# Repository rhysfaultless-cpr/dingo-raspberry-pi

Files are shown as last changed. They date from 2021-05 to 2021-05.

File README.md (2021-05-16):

# dingo-raspberry-pi
Installing a Raspberry Pi 4 on Clearpath Robotics Dingo

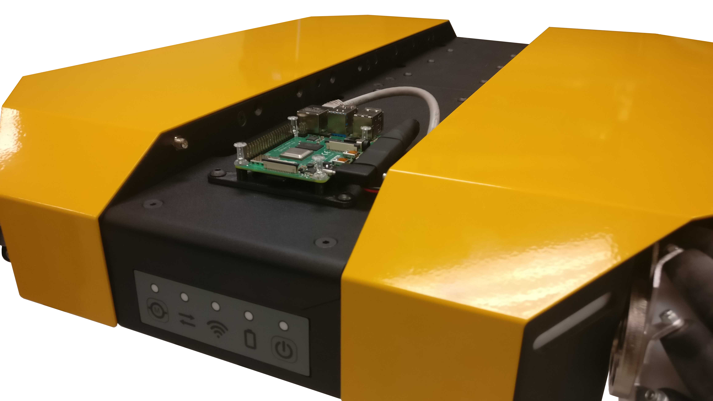
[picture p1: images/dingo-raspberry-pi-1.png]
Image of dingo and pi


Dingo is an indoor mobile robot that can be configured for differential-drive, or omnidrirectional-drive.
You can find more information about Dingo at the [Clearpath Robotics](https://clearpathrobotics.com/dingo-indoor-mobile-robot/) website.

## Hardware Overview

We mounted the Raspberry Pi 4 on the outside of the Dingo.
We conisdered this an advantage for the applications that want a low cost computer for Dingo.
The external mounting improves the Pi's WiFi signal, and gives quick access to the Pi's microSD card.

### Tools

You will need these tools:

* Wire stripper
* Wire cutter
* Crimper for Molex mini-fit-jr, 18 AWG crimps
* Hex key, 3 mm across flats

### Parts
| Quantity | CPR item number | Description | Manufacturer | Manufacturer # | Supplier | Supplier # |
| :---: | :--- | :--- | :--- | :--- | :--- | :--- |
| 1 | 021604 | microSD, 64 GB | Samsung | MB-ME64HA/AM | Amazon | B08879MG33 |
| 1 | 021758 | Cable—Ethernet, 2X RJ45, 300 | Monoprice | 13518 | — | — |
| 1 | 024011 | Bracket— Raspberry Pi | — | — | — | — |
| 4 | 024049 | Pin, Push | Westcott | 165841638 | Amazon | B003M5MTWC |
| 1 | 024051 | Computer, Single Board—Raspberry Pi 4, 4 GB | Raspberry Pi Foundation | Raspberry Pi 4 Model B, 4 GB | — | — |
| 1 | 024056 | Cable Assembly—USB-C X Molex | — | — | — | — |

#### 024011 Bracket— Raspberry Pi

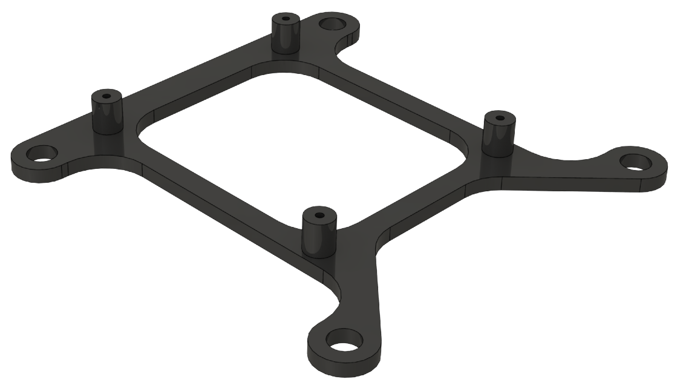
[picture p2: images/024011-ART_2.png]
Image of pi mounting bracket


This is a 3D printed bracket to hold the Pi on top of the Dingo. 
We printed our bracket in-house using PLA filament. ( fused deposition modeling, using polylactic acid filament )
A STEP214 model of this bracket is included in this repository as 024011-GEO_1.STL

#### 024056 Cable Assembly—USB-C X Molex 
(Raspberry Pi 4 Power Cable )

| Quantity | CPR item number | Description | Manufacturer | Manufacturer # | Supplier | Supplier # |
| :---: | :--- | :--- | :--- | :--- | :--- | :--- |
| 1 | 022206 | Connector, Housing | Molex | 39-01-2045 | Digi-Key | WM23701-ND |
| 2 | 022252 | Terminal, Crimp | Molex | 40-13-0852 | Digi-Key | WM24935-ND |
| 1 | 024192 | Cable—Barrel | Tensility | 10-02317 | Digi-Key | 839-1332-ND |
| 1 | 024193 | Connector, Adapter—USB-C to Barrel Female Ø2.1 X 5.5 | Adafruit | 4536 | Digi-Key | 1528-4536-ND |
| 1 | 024194 | Connector, Adapter—90° USB-C C USB-C | Adafruit | 4432 | Digi-Key | 1528-4432-ND |

### Hardware Installation Guide

These steps assume you have already printed the Pi's mounting bracket ( 024011 ), made the Pi's power cable ( 024056 ), and collected the parts and tools mentioned earlier.

0. Make sure your Dingo is turned off.
1. Remove the four round-head screws at the rear of the Dingo's trough cover.
2. Place the Pi mounting bracket ( 024011 ) over the four mounting holes. The bracket's flat section faces the rear of the Dingo.
3. Install the four round-head screws ( from step 1 ) into the Dingo's trough cover.
4. Place the Pi 4b onto the mounting bracket.
5. Install four push-pins into the mounting bracket.
6. Remove the Dingo rear trough cover's four flat-head screws.
7. Remove the Dingo's rear trough cover.
8. Connect the ethernet cable ( 021758 ) to the Dingo's MCU circuit board. 
Image of dingo MCU
9. Connect the power cable ( 024056 ) to the *PWR1* jack of the Dingo's MCU circuit board. This is a white jack in the centre of the circuit board.
10. Place the trough cover on the Dingo. The ethernet and power cable should pass through the trough cover's semi-circle cutout, so you can access the cables after fastening the cover.
11. Install four flat-head screws ( from step 6 ) into the trough cover.
12. Connect the power cable to the Raspberry Pi's USB type-C jack.
13. Connect the ethernet cable to the Raspberry Pi's RJ45 jack.

## Software Overview

We tested our Raspeberry Pi Dingo with Ubuntu server Bionic arm64.
Canonical will support this Raspberry Pi operating system until 2023.

### OS installation onto Pi
1. From your development computer, download [Ubuntu Bionic Raspberry Pi 3 (64-bit ARM)](http://cdimage.ubuntu.com/ubuntu/releases/18.04/release/ubuntu-18.04.5-preinstalled-server-arm64+raspi3.img.xz)
   You can see the similar images from Canonical [here](http://cdimage.ubuntu.com/ubuntu/releases/18.04/release/)
2. From your development computer, download and install [Raspberry Pi Imager](https://www.raspberrypi.org/software/)
3. Insert a 16 GB or larger microSD card into your development computer. We suggest the 64 GB card included in the parts list since this has sufficient speed, and additional storage for rosbags.
4. From your development computer, launch the Raspberry Pi Imager application.
5. In the Raspberry Pi Imager application:
   * Click *Operating System*
   * Select *Use custom* at the bottom of the OS list.
   * Select the OS downloaded in step 1. 
   * Clcik *Storage*
   * Select your micro SD in the storage options. 
   * Click 'Write'
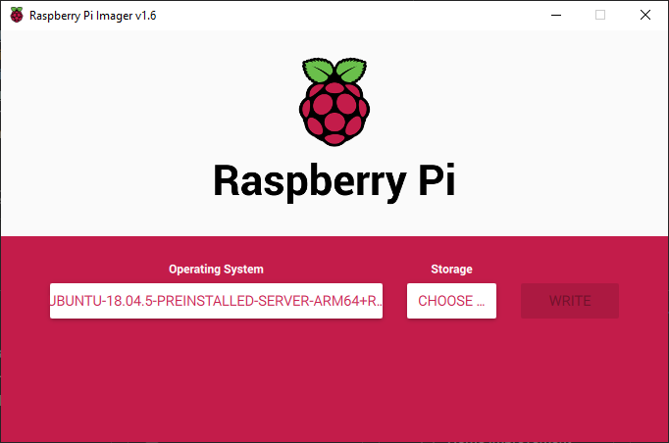
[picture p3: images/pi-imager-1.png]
Image of Pi imager 1


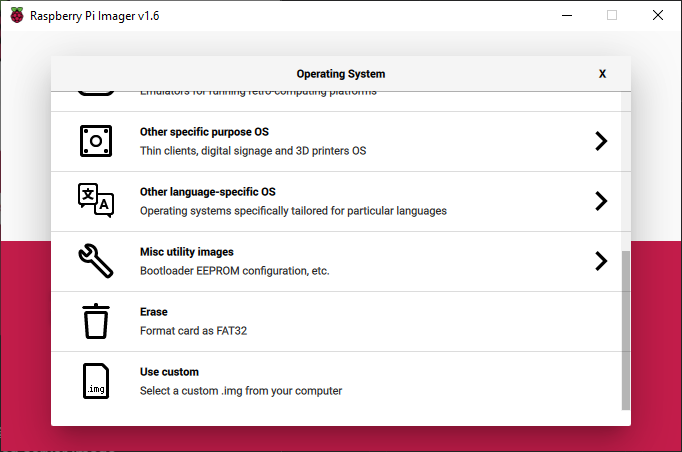
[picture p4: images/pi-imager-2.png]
Image of Pi imager 2


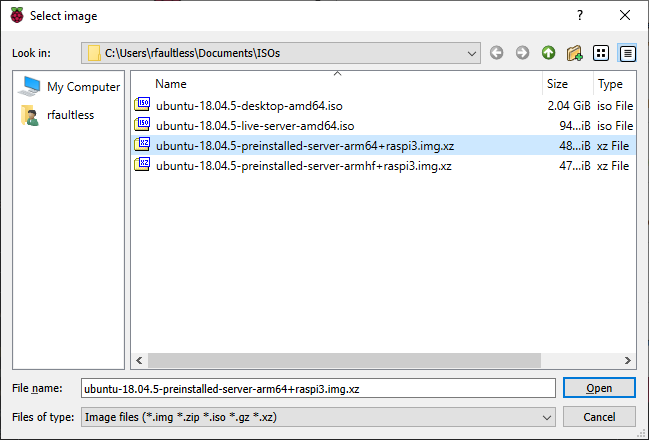
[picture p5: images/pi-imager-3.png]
Image of Pi imager 3


6. After the Raspberry Pi Imager finishes writing; remove the microSD card from your development computer.
7. Insert the microSD card into your Raspberry Pi 4.
8. Connect the following cables and then connect power to the Raspberry Pi:
   * RJ45 ethernet to an internet connection
   * HDMI to a monitor
   * USB keyboard
   * USB type-C power ( 3 A at 5 V )
9. Once the Pi has booted, enter the username and password: <br>
   `username: ubuntu ` <br>
   `password: ubuntu ` <br>
   `new password: choose a password ` <br>
10. Find the IP address of your Raspberry Pi: <br>
   `ifconfig `
11. From a terminal on your developement computer, SSH into the Pi:
   `ssh ubuntu@xxx.xxx.xxx.xxx`
   note: the Pi and your development computer will need to be on the same local-area-network.

### ROS installation
12. On your development computer's terminal, through SSH: <br>
   `wget -c https://raw.githubusercontent.com/clearpathrobotics/ros_computer_setup/main/install.sh && bash install.sh` <br>
   Note: this script is desribed [Clearpath ros_computer_setup](https://github.com/clearpathrobotics/ros_computer_setup)
   This script will ask you for the configuration of your Robot. 
   Select 2—Dingo, and 3—Jetson Nano.

### Network Configuration
13. Update Network Manager
   `sudo nano /etc/network/interfaces` <br>
    Change the first line to: <br>
   `auto lo br0 br0:0` <br>
    And comment out the line: <br>
   `allow-hotplug br0:0` <br>
14. Add Dingo Omni environment variable: <br>
   `sudo nano /etc/ros/setup.bash` <br>
    Adding a line to the end of the setup file if using a Dingo Omni, rather than a Dingo Differential: <br>
   `export DINGO_OMNI=1` <br>

### Bluetooth
This configuration is required if you want to use a Playstation Dualshock controller for controlling your Dingo.
This is specific to a Raspberry Pi, as the Raspberry Pi Foundation has set UART to controll GPIO pins by default, rather than bluetooth.
This change to use Dualshock controller will prevent you from using UART on GPIO pins 14 and 15 of your Pi.
You can review the reasoning described by the Raspberry Pi Foundation's [documentation](https://www.raspberrypi.org/documentation/configuration/uart.md).

15. Install Bluez:
   `sudo apt-get install bridge-utils ifupdown bluez-tools`
16. Update the Pi's boot configuration to set bluetooth as the primary UART device: <br>
   `sudo nano /boot/firmware/config.txt` <br>
    Comment out two lines: <br>
   `#enable_uart=1` <br>
   `#cmdline=nobtcmd.txt` <br>
    And add a line to the end of the file:` <br>
   `dtparam=krnbt=on` <br>
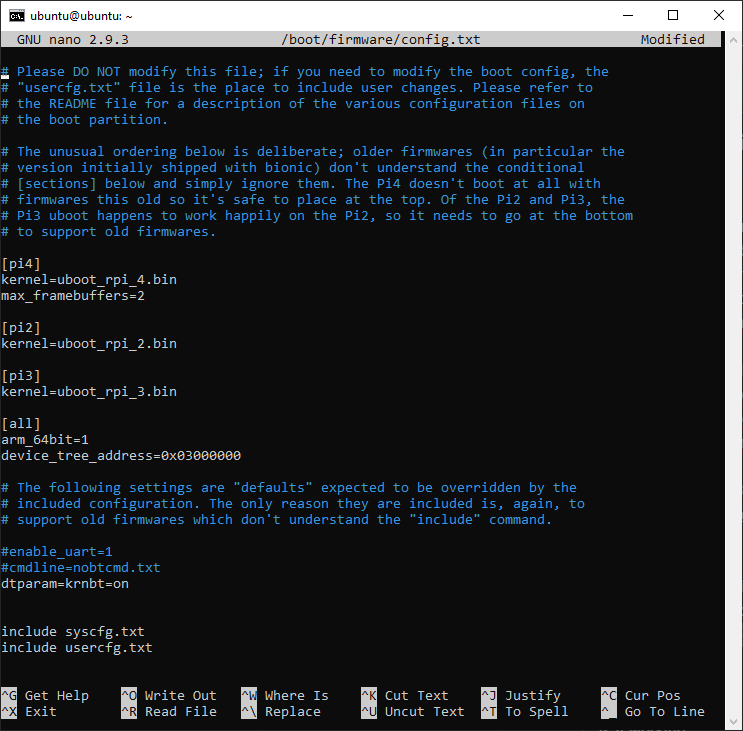
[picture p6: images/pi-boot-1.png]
Image of Pi boot config 1

17. `sudo nano /boot/firmware/syscfg.txt` <br>
    Comment out one line:  <br>
   `#include nobtcfg.txt` <br>
    And add a line:  <br>
   `include btcfg.txt` <br>
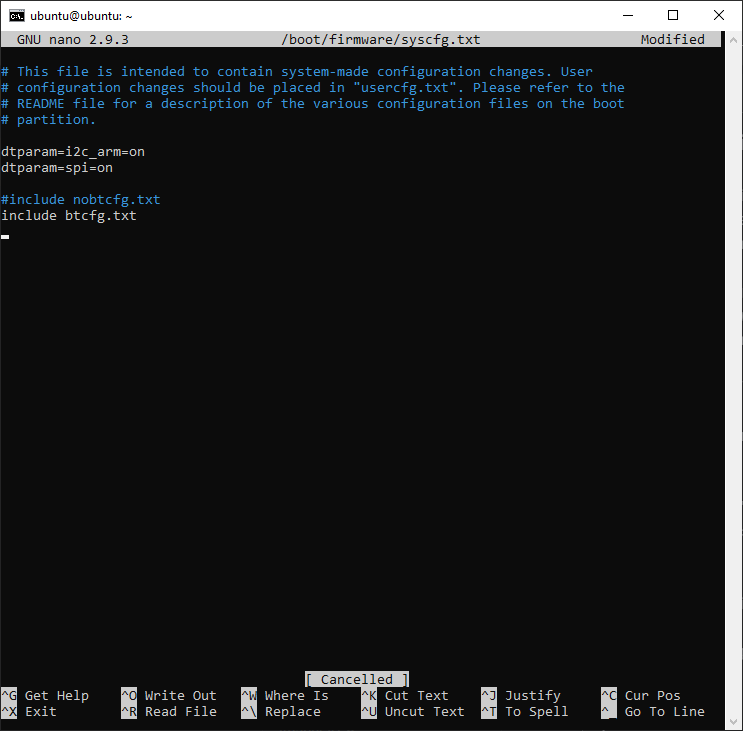
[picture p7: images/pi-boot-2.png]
Image of Pi boot config 2


18. Install bluetooth for Raspberry Pi:
   `sudo snap install pi-bluetooth`
19. update and reboot:
   `sudo apt update && sudo apt upgrade`
   `sudo reboot now`

### Bluetooth Dualshock Controller Pairing
20. `sudo bluetoothctl` <br>
   `# scan on` <br>
    On the PS4 controller, hold 'SHARE' and the 'PS' button till the top light blinks twice then a pause, repeatedly.
    Your PS4 controller's address should appear on the termainal. 
    Mine was 'AE:11:58:60:5F' which you will see in the following steps. <br>
   `#pair A4:AE:11:58:60:5F` <br>
   `#trust A4:AE:11:58:60:5F` <br>
   `#connect A4:AE:11:58:60:5F` <br>
    You may need to press the PS button on the controller again during the process due to a timeout.

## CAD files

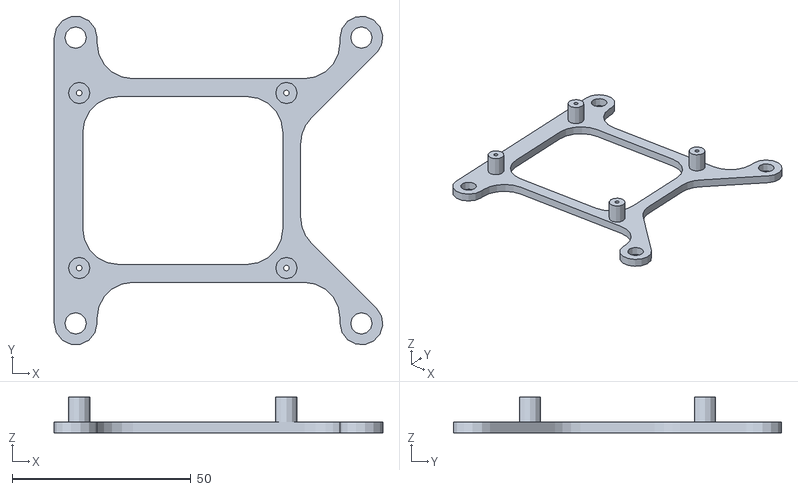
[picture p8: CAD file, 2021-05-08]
hardware/024011-GEO_1.STL
92.0 x 91.8 x 10.0

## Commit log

2021-05-08 updated README with an overview of the repo, and with tools required to install a Pi
    [024011-GEO_1.STL]
2021-05-09 added cable BOM to the README.
2021-05-09 added overall BOM to the README.
2021-05-09 adjusted # subsection for 024056 cable.
